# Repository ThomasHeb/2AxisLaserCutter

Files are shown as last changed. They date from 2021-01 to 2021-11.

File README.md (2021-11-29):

## What is new?
- G0 commands for seeking with laser off implemented (for use with Lightburn software)

## What is coming next?
- Please let me know, if you have ideas or need improvements

# 2AxisLaserCutter

- Arduino based CNC laser cutter with display and SD-Card.
- Shared firmware with [4AxisFoamCutter](https://github.com/ThomasHeb/4AxisFoamCutter)
- Ruby Script for SketchUp Make 2017 to generate gcode.

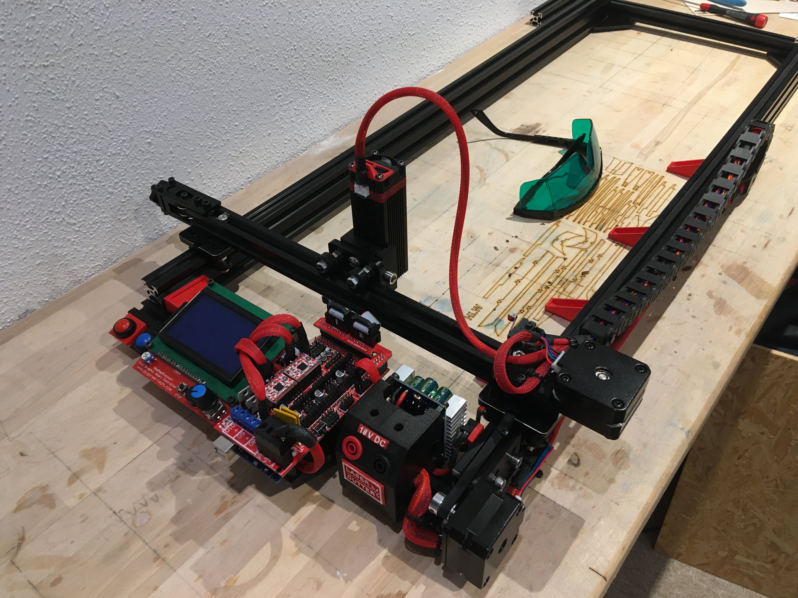
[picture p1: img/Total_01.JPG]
Total_01


My goal was to build semi scale balsa glider based on old fmt plans. It is a lot of effort to copy the plans on the balsa, cut it, and sand it. Especially for small models, very accurate working is necessary. This brought my to the idea to build a laser cutter and do the glider design in SketchUp. 

The base idea ist very simple. Two independent linear axis with NEMA 17 stepper and belts on 2020/2040 v-slot rails and Arduino Mega / Ramps, based on a modified grbl 8c2, which I am using in my FoamCutter, too. There are some special requests for the grbl, when working with a laser, especially when using as an engraver. The firmware modifications will be mentioned in the „Firmware“ section below.

I have a lot old paper plans for gliders. So I take some photos of the plans, imports these to SketchUp Make 2017, redraw and scale the plan. For generating the gcode, I wrote a small script. Description is below in section „Working with SketchUp“.

# Safety
Due to the specific characteristics of laser radiation and the biological and physical effects this has, special protection and cautionary measures are required in the use of lasers.
- Do not look into the beam or direct reflections, also do not look with optical instruments.
- wear special protection googles for the laser you are using
- Clear marking of the laser area with warning signs at all access points.
- Route the laser beam clearly below or above eye level, but not at eye level.
- Refer to the manuals and safety instructions of your laser module
- Refer to the manuals and safety instructions of other used equipment (Ramps, Arduino, DC/DC Converter, power supply, …)
- Please keep all standards and safety topics in mind, when handling with high voltage on power supply, best is to contact an authorised specialist.

# Videos
- [Video tutorial](https://youtu.be/N7kasb9n7cc)

# Mechanics
- 2x linear v-slot actuator with NEMA 17 stepper
- 2020 and 2040 profiles, screws, nuts
- plates for stepper and connecting the profiles 
- Neje Laser
- 3D-printed parts for mounting the hardware on the rails

A bill of material (including hardware and electronics) and detailed photos are in the folder [01_Mechanics](https://github.com/ThomasHeb/2AxisLaserCutter/tree/main/01_Mechanic)

# Hardware

- Arduino Mega with Ramps 1.4 board
- Display and SD card reader for loacl operation

A block diagramm is provided in the folder [02_Hardware](https://github.com/ThomasHeb/2AxisLaserCutter/tree/main/02_Hardware)

# Firmware

- The Firmware is based on GRBL 8c2 
- Special modifications for local operation
- Special operation for synchron power regulation of the laser 

More Details here: [03_Firmware](https://github.com/ThomasHeb/2AxisLaserCutter/tree/main/03_Firmware)

# First operation / setup
In this chapter you find some recommendations how to get started and how to setup the laser cutter.

## First test of Arduino.
The Arduino and the Ramps board are working without the stepper driver or motors.
- Mount the Ramps on the Arduino
- Connect the display to the Ramps
- Connect the Arduino with the USB
- Connect to USB and load the firmware and check if you get a welcome screen (you need an Arduino IDE installed).

## Adjusting and first operation of stepper
- Adjust the driver [link](https://www.makerguides.com/a4988-stepper-motor-driver-arduino-tutorial/)
- Place the jumper and the stepper driver on the Ramps
- Connect the NEMA 17 stepper motor to E0 / E1
- Connect 12V DC to Ramps 3/4
- Connect the Arduino to USB. 
- Go to position menu and check the operation of the stepper motor
- Disconnect power supply and USB

## Operation of limit switches and e-stopp
- Place each a jumper on S and - for X- and X+
- Connect 12V DC to Ramps 3/4
- Optional: Pull one jumper, Arduino should go to Error. Reset the Arduino
- Optional: Pull the other jumper, Arduino should go to Error. Reset the Arduino
- Connect D68 to GND, Arduino should go to Error
- Disconnect power supply and USB

## Mechanic meets hardware
- Assemble the mechanic 
- Connect the hardware
- Do NOT connect the laser
- Wire the NEMA 17 stepper motor
- Optional: Wire the limit switches
- Wire the e-stopp
- Connect 12V DC to Ramps 3/4
- Connect the Arduino to USB. 
- Go to position menu and check movement of the axis
- Check direction of the axis, 
  - Otherwise open the parameters in the Serial Monitor of the Arduino IDE with $$
  - Adjust parameter $7
- Calculate the Steps per mm, adjust parameter $0 and $1
  - Equation is : (USER_STEP_PER_REVOLUTION x USER_MICROSTEPS) / (USER_PITCH_BELT x USER_GEAR)
  - Example: (200 steps/rpm x 16 Microsteps) / (2mm x 20) = 80
  - Best is to adjust the defaults.h, compile and download and set parameter to default with $R
- Operate the e-stopp, Arduino should go to Error. Reset the Arduino
- Optional: Operate the limit switches, Arduino should go to Error. Reset the Arduino
- Optional using limit switches: Go to homing menu and start a homing cycle. 
  - Check if axis are moving to the right direction, otherwise adjust parameter $19
- Check and adjust other parameters. refer to grbl parameter settings online.
- Disconnect power supply and USB

## First operation of the laser
- Assemble and connect the laser
- Operate all the safety measures / steps required, refer to the safety instructions and manuals of your laser
- Connect 12V DC to Ramps 3/4
- Go to position menu and toggle the laser dot. you should see a laser to on your table (0.2% of laser power, you can change this in defaults.h, DEFAULT_LASER_DOT, compiler run and firmware upload is required)
- adjust the focus of the lens of your laser
- Operate the e-stopp, Arduino should go to Error, laser should switch off. Reset the Arduino
- Optional: Operate the limit switches, Arduino should go to Error, laser should switch off. Reset the Arduino
- Optional using limit switches:
  - Go to position menu and toggle the laser dot on.
  - Move the laser to your prefers mechanical zero position.
  - Push the back button (stop button on display)
  - Go to homing menu and select "set as new pull-off?", acknowledge by pushing the rotary knob
  - This position is stored and accessed with the next homing cycle

## Find best settings for the laser
- To achieve good cutting results, you must find the right settings for each material type and thickness
- I recommend to start with a 2mm balsa sheet
  - Take a 1mm balsa sheet and adjust the focus of the laser in the position menu with the dot
  - Make several test cuts with different power settings and feed speeds and repeats
  - A good result is where the complete wood is cut through and corners are sharp
  - My preferred setup is 2xS40F400 (2 repeats with 40% power and a feed rate of 400mm/min), or 3xS40F500, especially when the density of the balsa is a bit higher
  - The resulting dimension is at the beginning not very important, because this can be adjusted in the design.
  - You can use the "test_01.gcode" file from the [06_Example](https://github.com/ThomasHeb/2AxisLaserCutter/tree/main/06_Example) folder (1xS15F500 is used for the text)
  - You can generate your own test pattern with SketchUp and the laser cutter script.
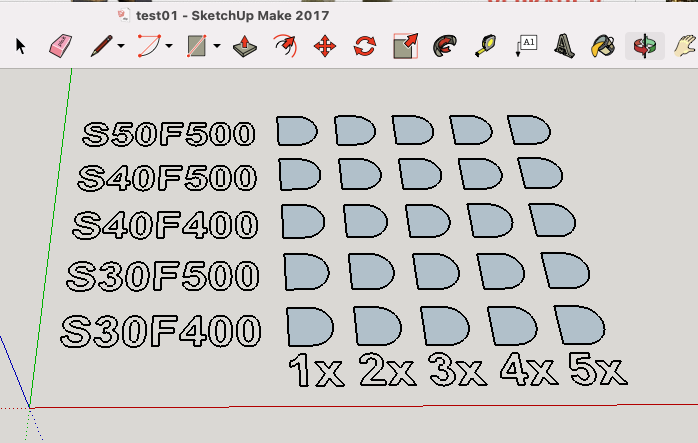
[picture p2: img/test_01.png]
Test_01
    
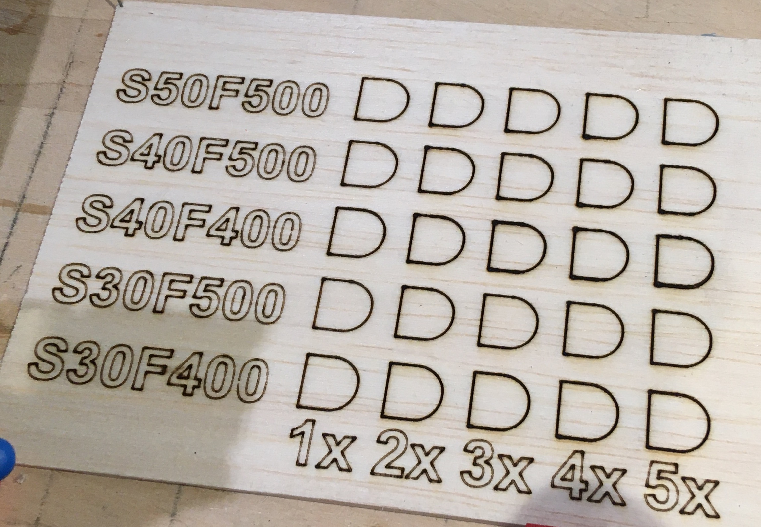
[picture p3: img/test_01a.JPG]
Test_01a
    
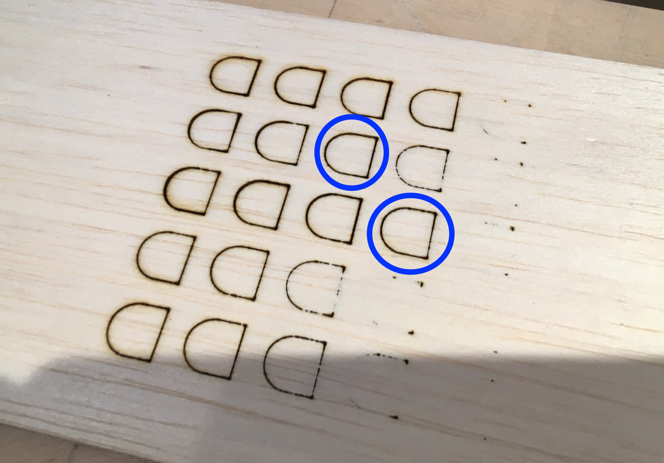
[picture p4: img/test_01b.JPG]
Test_01b
    

# SketchUp Script
I use SketchUp for generating the stl-files for my 3D printed parts. I decided to write a small script which allows me to generate gcode for laser cutting. Currently I use only linear extrapolation in combination. The results are good.

## What you need
- SketchUp (I am using SketchUp Make 2017)
- Ruby Code Editor
- Download lasercutter.rb from the code section

## Functionality and usage of laser.rb
- Download the script from the folder /04_SketchUp/lasercutter.rb
- Open the ruby code editor first and load and execute the lasercutter.rb. This adds 2 menus to the PlugIn menu.
  - LaserCutter Settings: you can define some general settings, like inch/mm, used decimals.
  - LaserCutter Tool: Generates gcode for all selected edges and face surfaces and exports it. 
    - The red axis is used as horizontal
    - The green axis is used as vertical 
    - The algorithm converts surfaces to surrounding edges
    - Searches all edge and generates gcode along the edges
    - There is no algorith for optimizing travel distances

## Check out the tutorial video
- [Video tutorial](https://youtu.be/N7kasb9n7cc)

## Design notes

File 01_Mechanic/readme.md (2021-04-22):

# Mechanics

Total_01

I use 800mm 2040 v-slot rails, which gives me a operation length of app. 680mm (x-axis) and 350mm 2020 v-slot rails, which allows me to travel app. 200mm in depth (y-axis). You can change the length of the rails according to your required working dimensions.
Including stepper, arduino, you might invest app. 340 EUR. For the 3D-printed parts, additional costs have to be considered.
Please be aware, that you can buy laser engraver in complete kits at app. 200 EUR. So I recommend this project only, if it is about building something from scratch.

# Bill of Material
- 2x [800mm 2040 v-slot rail](https://de.banggood.com/Machifit-100-1000mm-Black-2040-V-Slot-Aluminum-Profile-Extrusion-Frame-for-CNC-Tool-DIY-p-1342020.html?ID=527877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)
- 3x [350mm 2020 v-slot rail](https://de.banggood.com/Machifit-Black-2020-V-Slot-Aluminum-Profile-Extrusion-Frame-for-CNC-Laser-Engraving-Machine-p-1341703.html?ID=515970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)
- 4x [90° Connector plate](https://de.banggood.com/Machifit-5-Holes-Aluminum-Profile-Connector-Joint-Plate-Corner-Bracket-for-2020-Aluminum-Profile-p-1350953.html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)
- 2x [NEMA 17 mounting plate](https://de.banggood.com/Machfit-Aluminum-Nema-17-Stepper-Motor-Mount-Plate-for-CNC-Machine-V-slot-Aluminum-Extrusions-Profile-CNC-Parts-p-1470310.html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)
- 2x [Idler pully including plates](https://de.banggood.com/TWO-TREES-Black-2020-Profile-X-axis-Synchronous-Belt-Stretch-Straighten-Tensioner-for-3D-Printer-p-1581141.html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)
- 3x [Gantry Plate](https://de.banggood.com/Machifit-V-Slot-V-Gantry-Plat-Special-Slide-Plate-Five-Roulette-for-2040-Aluminum-Profile-p-1380194.html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)
- 1x Bag [Nuts 5mm](https://de.banggood.com/Drillpro-50pcs-M5-T-Sliding-Nut-Zinc-Plated-Carbon-Steel-T-Sliding-Nut-for-2020-Aluminum-Profile-p-1048439.html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)
- 1x Bag [Nuts 5mm](https://de.banggood.com/Drillpro-100pcs-M5-Hammer-Nut-Nickel-Plated-Carbon-Steel-Aluminum-Connector-T-Fastener-Sliding-Nut-p-1048442.html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)
- 1x Bag [Nuts 3mm](https://de.banggood.com/Drillpro-50pcs-M3-T-Sliding-Nut-Zinc-Plated-Carbon-Steel-T-Sliding-Nut-for-2020-Aluminum-Profile-p-1081131.html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)
- 1x Bag (2 needed) [Limit Switch](https://de.banggood.com/10Pcs-Micro-Limit-Switch-Roller-Lever-5A-125V-Open-Close-Switch-p-945733.html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)
- 1x [red button for stopp operation](https://de.banggood.com/Car-Auto-Momentary-OFF-ON-Push-Round-Button-Horn-Switch-Multicolor-p-927835.html?ID=224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)
- 1x optional [blue button for back operation](https://de.banggood.com/Car-Auto-Momentary-OFF-ON-Push-Round-Button-Horn-Switch-Multicolor-p-927835.html?ID=224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)
- 2x [NEMA 17 Stepper](https://de.banggood.com/17HS4023-12V-Nema-17-2-Phase-Stepper-Motor-For-Extruder-3D-Printer-Motor-p-1368552.html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)
- 1x Pack [Pully 20T + Belt GT2](https://de.banggood.com/20T-GT2-Aluminium-Timing-Pulley-2GT-5M-Belt-For-RepRap-Prusa-Mendel-3D-Printer-p-1081330.html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)
- 1x [Arduino Mega, Ramps 1.4, Stepper Driver](https://www.amazon.de/Drucker-1-4-Controller-Mega2560-R3-A4988-mit-Kühlkörper/dp/B07DJ3WBCP/ref=sr_1_1_sspa?__mk_de_DE=ÅMÅŽÕÑ&dchild=1&keywords=ramps+1.4)
- 1x [Display](https://www.amazon.de/Redrex-Vollgrafik-Display-Controller-3D-Drucker-Arduino/dp/B01LO20XGS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)
- ALTERNATIVE [Arduino, Mega, Ramps 1.4, Stepper Driver, Display](https://de.banggood.com/Geekcreit-LCD-12864-RAMPS-1_4-Board-2560-R3-Control-Board-A4988-Driver-Kit-For-3D-Printer-p-936768.html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)
- 1x [Neje 20W 450nm Lasermodule](https://de.banggood.com/NEJE-20W-Laser-Module-DIY-Kit-450nm-Professional-Continuous-5_5W-Laser-Cutting-Engraving-Module-Blue-Light-with-TTL-or-PWM-Modulation-for-Las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)
- 1x optional [DC DC Converter](https://www.amazon.de/gp/product/B00HV4EPG8/ref=ppx_yo_dt_b_asin_title_o01_s01?ie=UTF8&psc=1)
- 1x optional [red and black connector](https://www.amazon.de/GTIWUNG-Bananenbuchse-Bananensteckdose-Verstärkeranschluss-Bananenstecker)
- optional 3D printed parts, see SketchUp or stl-file in 01_Mechanic folder
- 1x optional [inlay nuts (1 box)](https://www.amazon.de/gp/product/B082KFQV71/ref=ppx_yo_dt_b_asin_title_o03_s00?ie=UTF8&psc=1) for 3D printed parts
- M5, M3, M2.5, M2 screws

# Assembly

You find a lot of pictures in the [img folder](https://github.com/ThomasHeb/2AxisLaserCutter/blob/main/img/).

Recommendation: Connect and wire the hardware (Arduino, Ramps, stepper, laser, …) first and test it. Refer to chapter [„Hardware“](https://github.com/ThomasHeb/2AxisLaserCutter/tree/main/02_Hardware) and chapter „First operation / setup“.

## Y-Axis
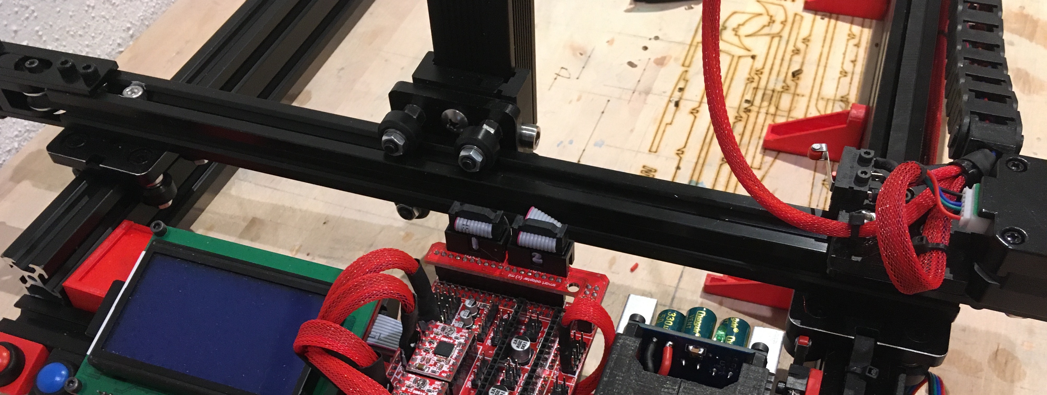
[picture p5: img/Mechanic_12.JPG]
Mechanic_12


### Parts
- 1x 350mm 2020 v-slot rail
- 1x NEMA 17 mounting plate
- 1x Idler pully including plates
- 3x Gantry Plate
- 1x NEMA 17 Stepper
- 1x Pully + Belt
- 1x optional 3D printed "combi holder"
- 1x optional limit switch
- 1x mounting plate for Neje laser (included in laser kit)
- 1x Neje laser

### Steps
- Drill a hole in one gentry plate to fix the laser mounting plate.
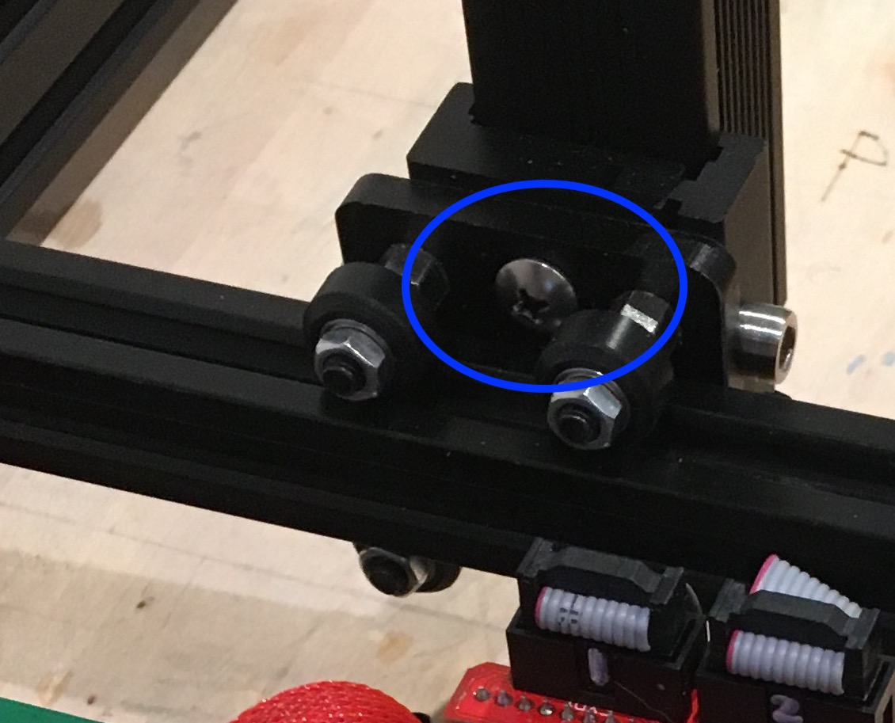
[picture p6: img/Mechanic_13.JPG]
Mechanic_13
  

- Drill a hole in the 2020 v-slot rail to fix the gentry.
- Mount the idler pully.
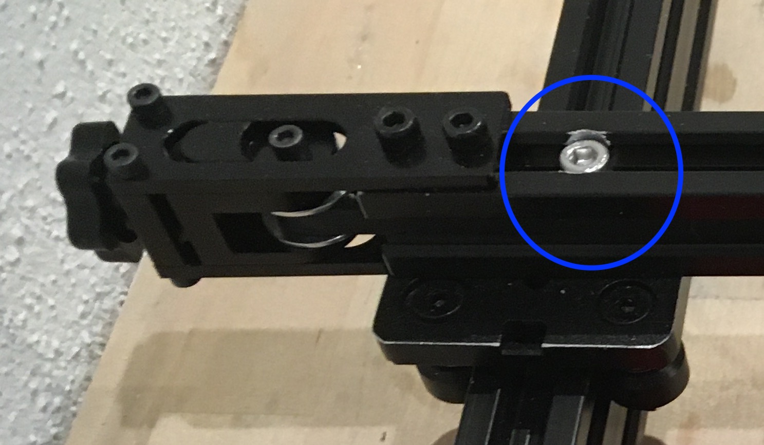
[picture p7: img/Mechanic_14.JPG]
Mechanic_14
  

- Drill two holes (blue) in the 2020 v-slot rail to fix the gentry together with the motor mounting plate
- Optional: Drill two holes (mangenta) in the motor mounting plate and cut a threat to fix the combi holer (3D print)
- Optional: Mount the combi holer (3D print) and the limit switch
- Mount the stepper and the pully and the belt
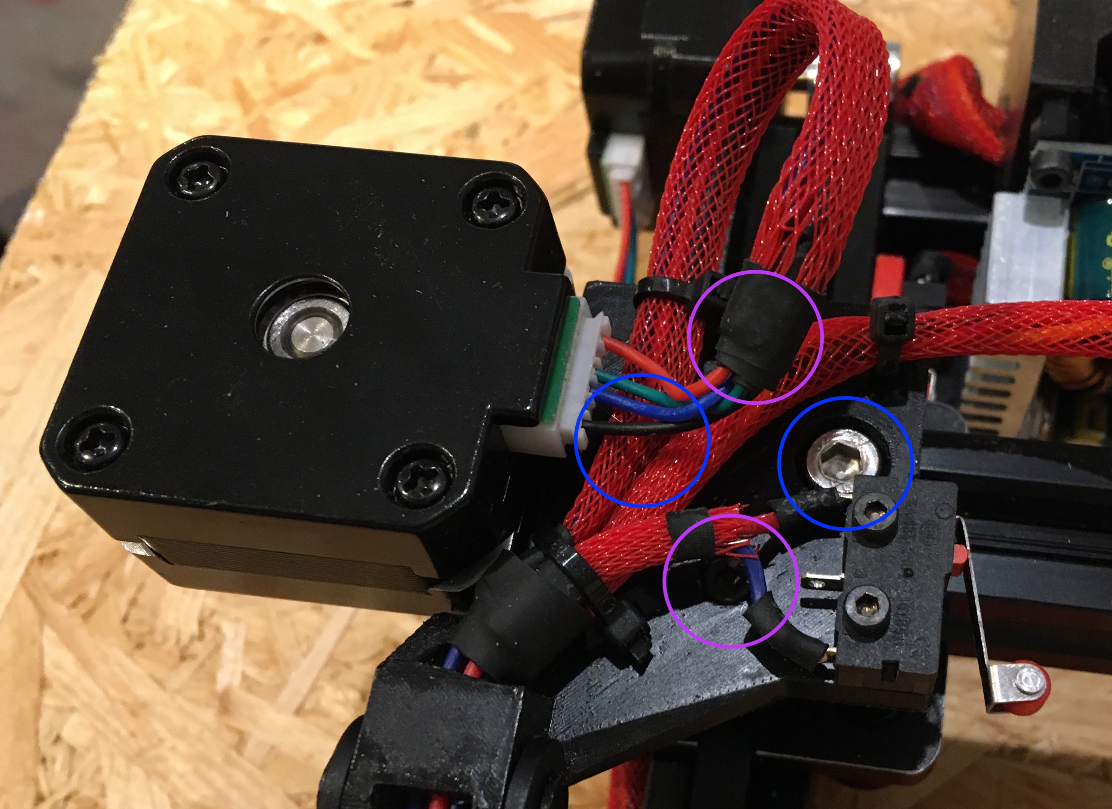
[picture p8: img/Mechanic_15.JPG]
Mechanic_15
  

- You may change the screw for clamping the laser or sand it down a bit, so that the mouinting plate lies flat on the gentry 
- Optional: Mount the cable clamp on the laser (3D print)
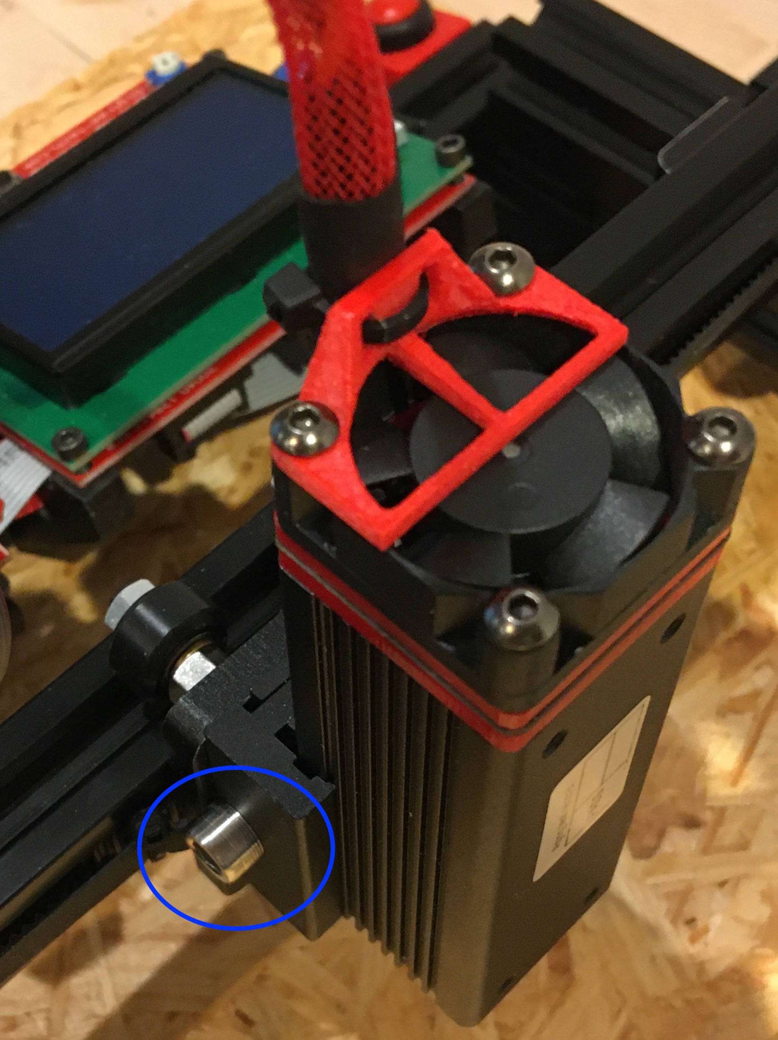
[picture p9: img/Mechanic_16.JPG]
Mechanic_16
  

## X-Axis
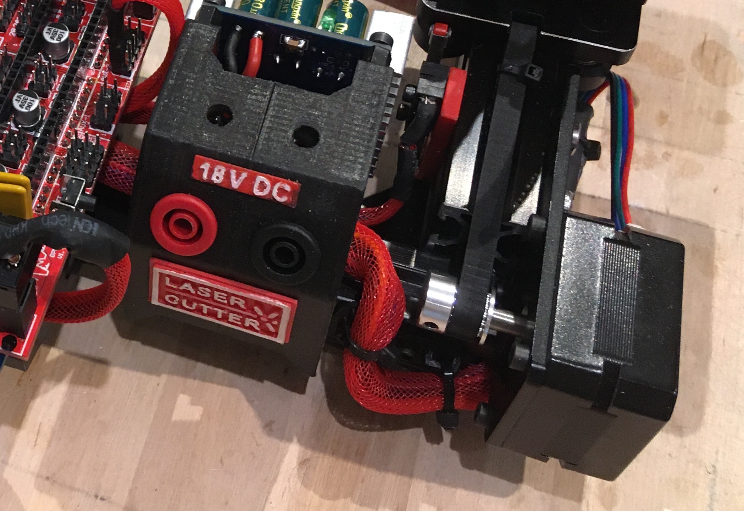
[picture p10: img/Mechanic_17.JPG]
Mechanic_17


### Parts
- 2x 800mm 2040 v-slot rail
- 1x NEMA 17 mounting plate
- 1x Idler pully including plates
- 1x NEMA 17 Stepper
- 1x Pully + Belt
- 1x optional 3D printed "holder cable chain"
- 1x optional 3D printed "holder limit switch"
- 1x optional limit switch

### Steps
- Mount the motor plate with the NEMA 17 stepper
- Add the Y-Axis
- Mount the idler pully.
- Optional: Mount the limit switch and the limit switch holder
- Optional: Mount the holder for the cable chan and the cable chain itself
- Mount the pully and the belt
- Add the second 800 v-slot rail to the idler gentry
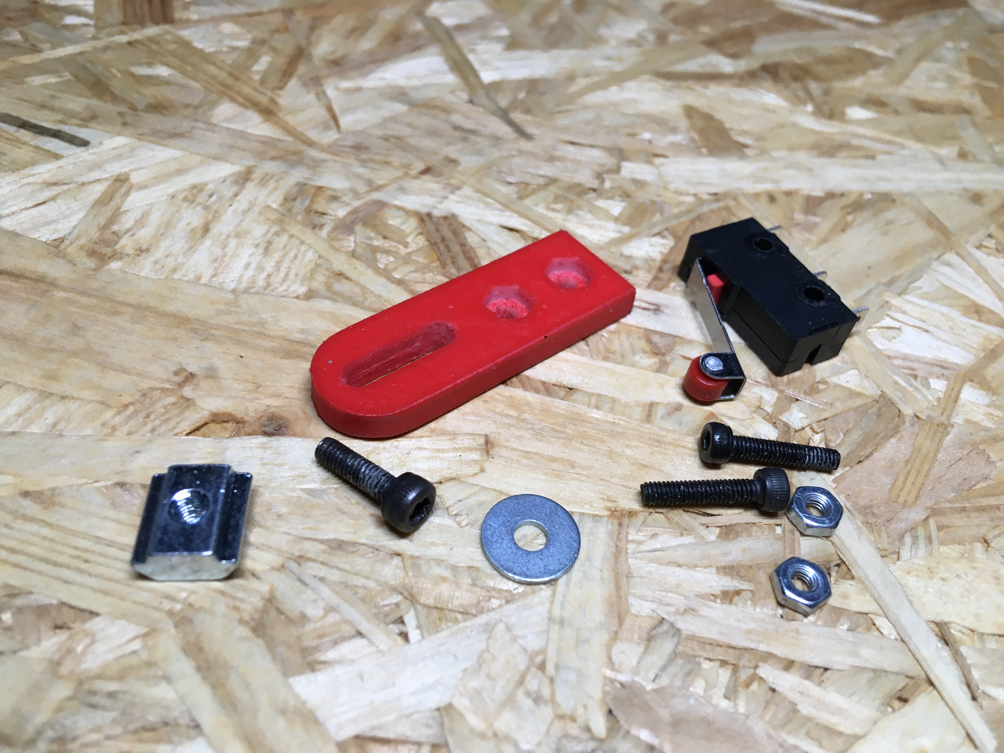
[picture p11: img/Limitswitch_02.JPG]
Limitswitch_02
  
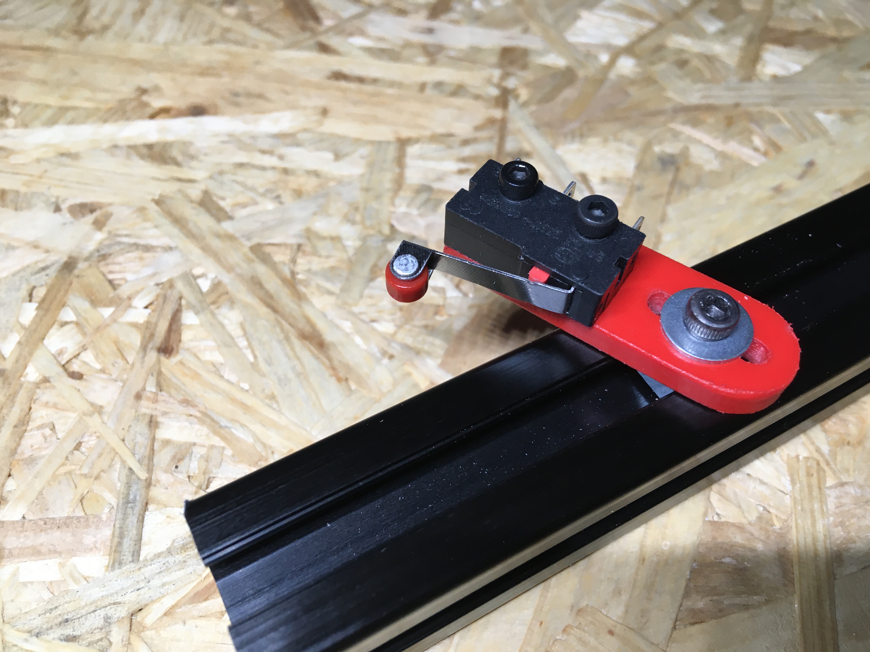
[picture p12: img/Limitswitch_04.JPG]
Limitswitch_04
  
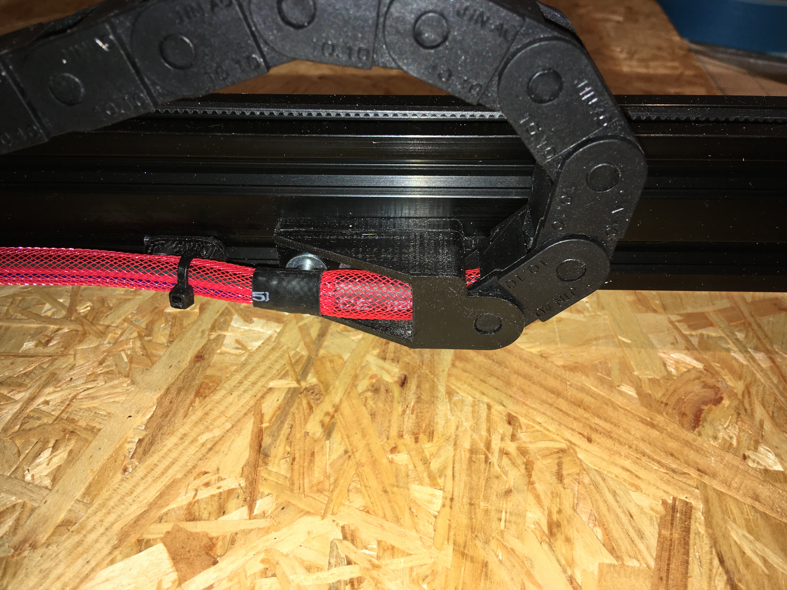
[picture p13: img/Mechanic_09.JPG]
Mechanic_09
  

## Connection rails with electronic
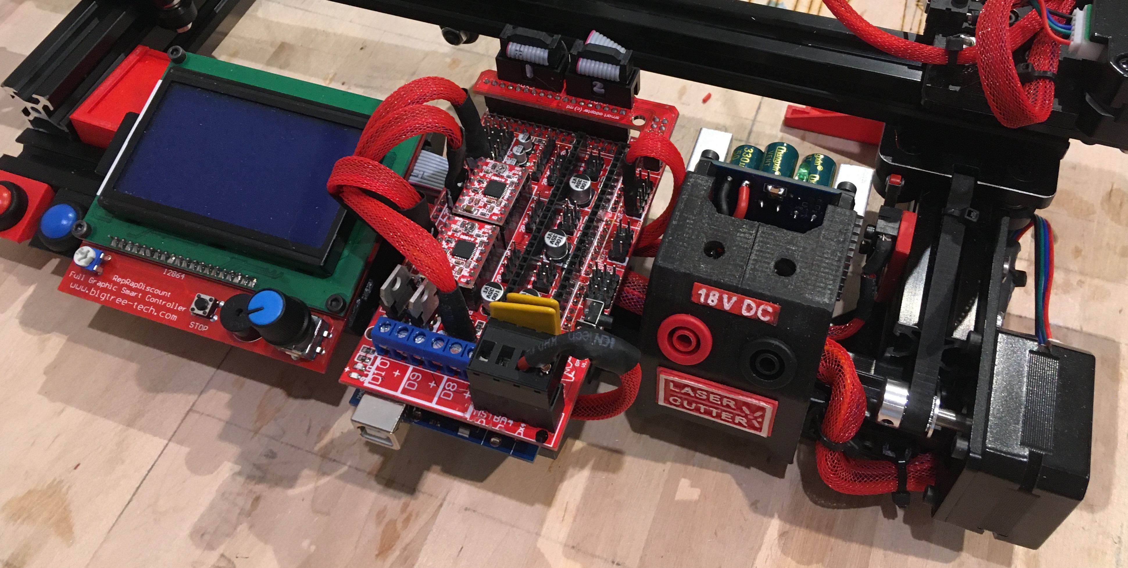
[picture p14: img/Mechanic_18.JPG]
Mechanic_18


### Parts
- 2x 350mm 2020 v-slot rail
- 4x 90° Connector plate
- 1x Arduino Mega
- 1x Display
- 1x Ramps
- 1x optional DC DC Converter
- 1x optional red and black connector
- 1x optional blue button
- 1x red button
- 3D printed holder with inlay nuts

### Steps
- Mount the 90° connector plates on the edges of the 800mm 2040 v-slot rails
- Connect the two rails with a two 350mm 2020 v-slot rails (these rails need to be cut)
- Next to the motor mounting plate of the x-Axis: Make some space for the screw
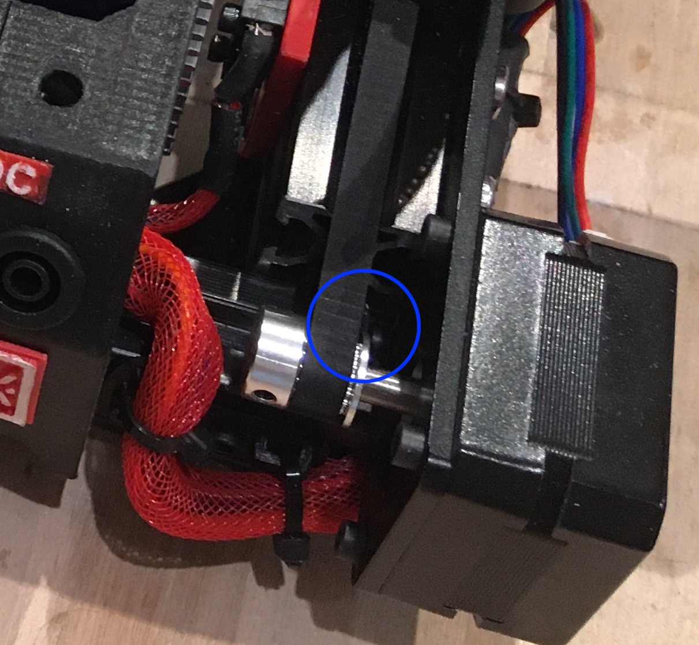
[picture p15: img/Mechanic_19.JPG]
Mechanic_19
  
- Mount the 3D printed holders for display, buttons, Arduino/Ramps and power connection (different options available, see SketchUp file / stl-files)
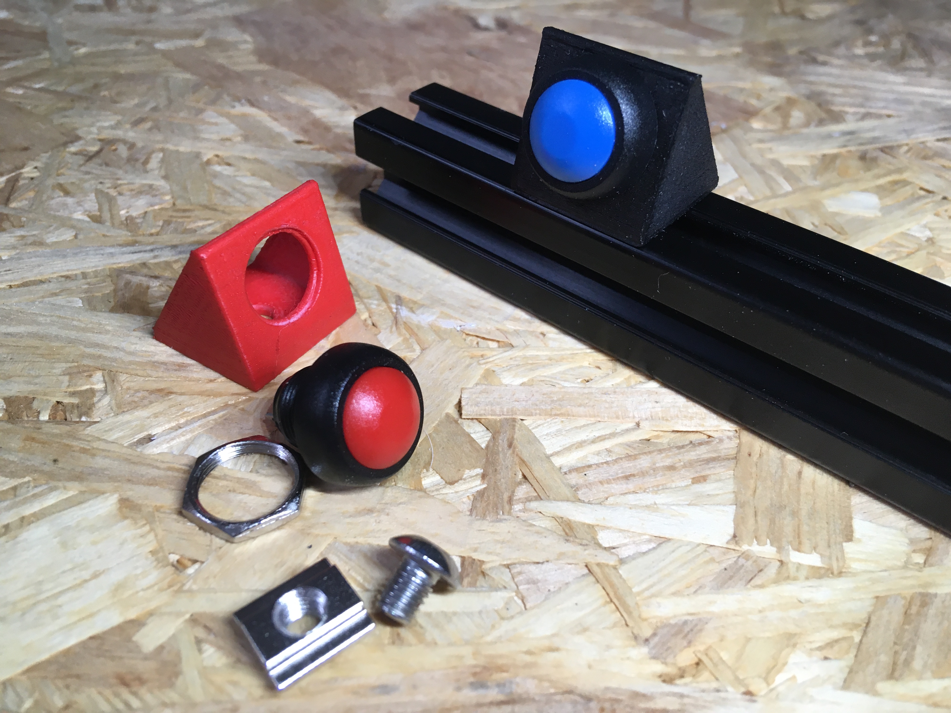
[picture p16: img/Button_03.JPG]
Button_03
  
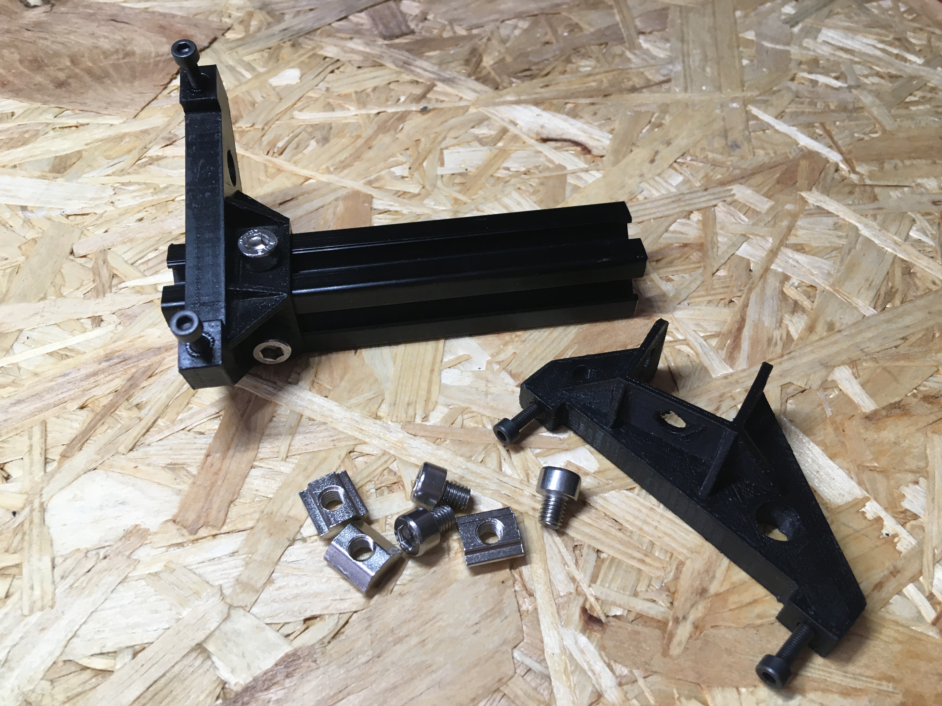
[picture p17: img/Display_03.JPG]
Display_03
  
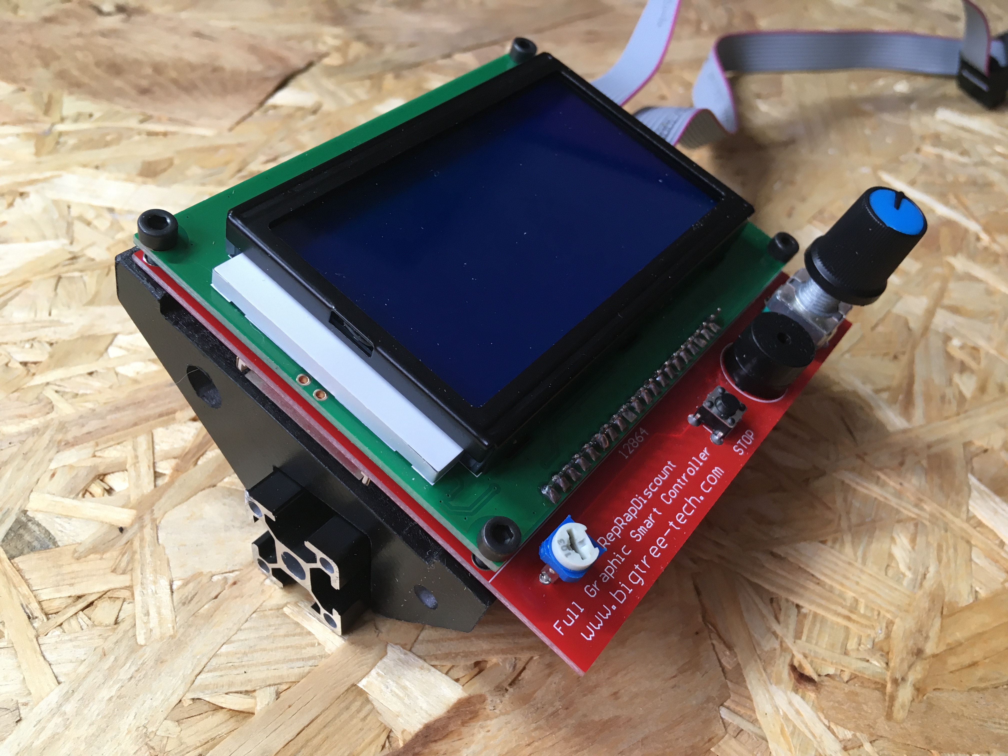
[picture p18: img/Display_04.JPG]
Display_04
  
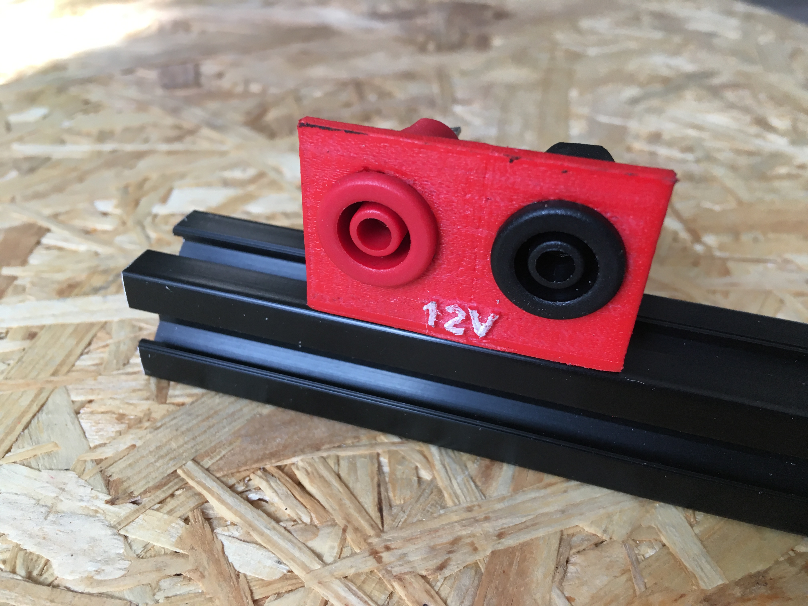
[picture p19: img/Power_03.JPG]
Power_03
  
- For wiring, see Section [02_Hardware](https://github.com/ThomasHeb/2AxisLaserCutter/tree/main/02_Hardware)

## Final
Before tightening all screws, please ensure that all axis and the laser it self are orientated in a 90° angle, all movements are smooth.

[Back to main page](https://github.com/ThomasHeb/2AxisLaserCutter)

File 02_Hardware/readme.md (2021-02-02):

# Hardware

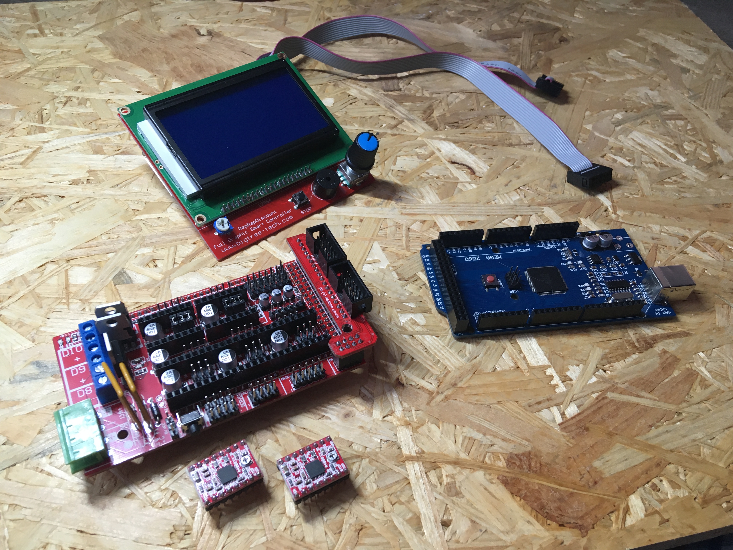
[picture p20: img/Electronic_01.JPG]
Electronic_01


The hardware is based on Arduino Mega with display and Ramps 1.4 Board. Ramps 1.6 and similar boards will work, too.

# Modifications
- Add a 100nF C between S and GND for the X and Y limit switches
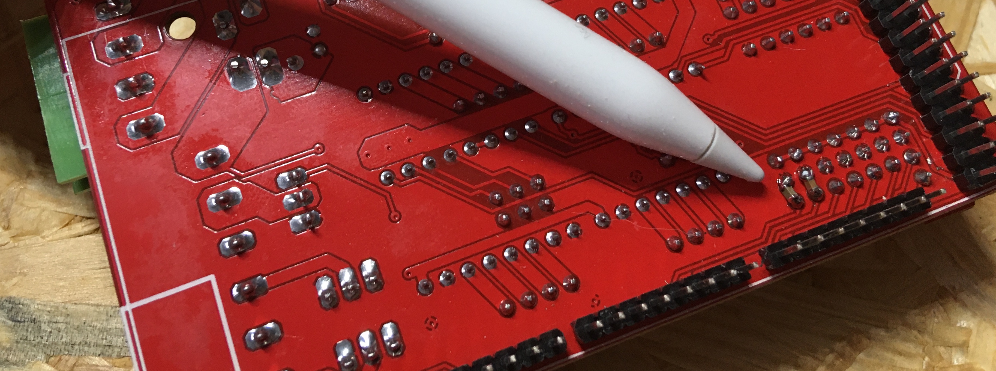
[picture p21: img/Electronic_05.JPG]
Electronic_05
  
- Add a 100nF C between D63 and GND for the e-stopp button
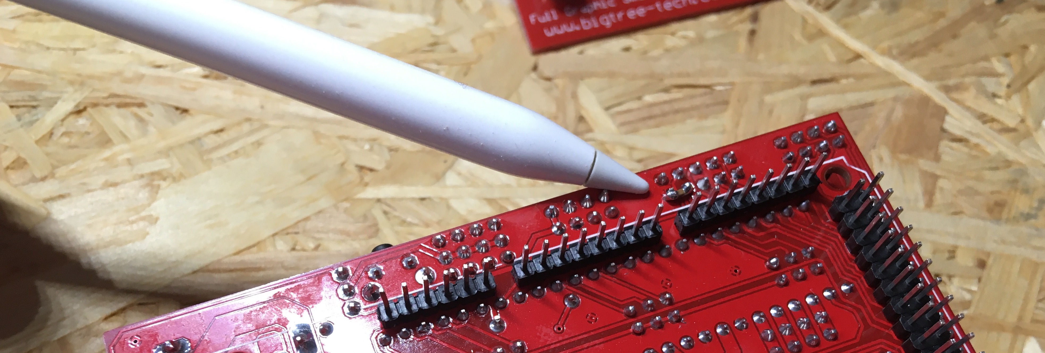
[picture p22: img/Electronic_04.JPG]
Electronic_04
  

- Optional: When using an external back button, connect the button by soldering wires parallel to the stop button on the display, otherwise the stop button on the display operates as back button.

# Blockdiagram / Connections

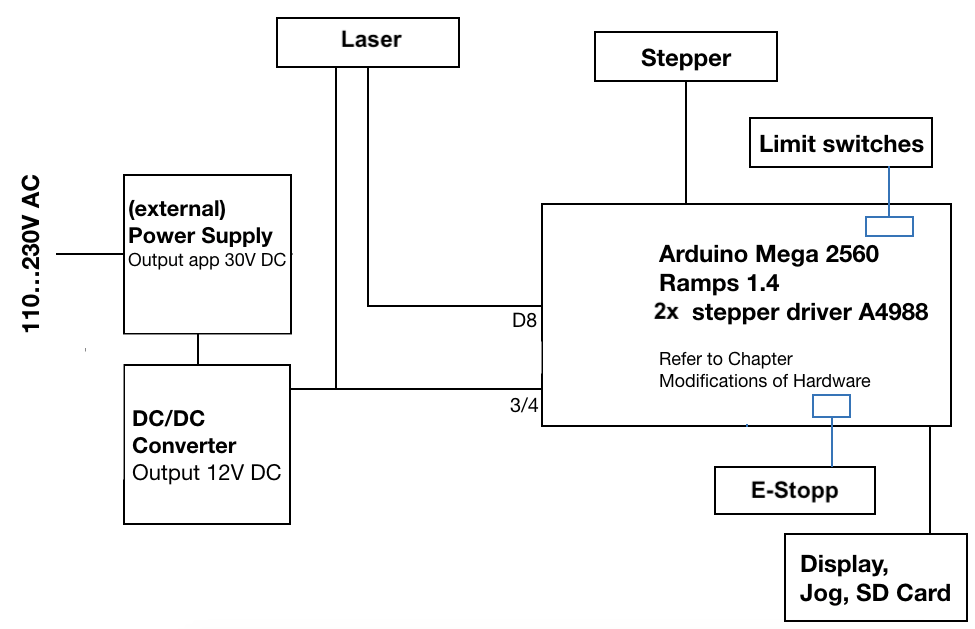
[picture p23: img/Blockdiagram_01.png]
Blockdiagram_01
  
- Stepper X-axis on E0 socket on Ramps // 1/16 Microsteps (set all three jumpers)
- Stepper Y-axis on E1 socket on Ramps // 1/16 Microsteps (set all three jumpers)
- Optional limit switch X-axis on X- S/- on Ramps (1st from left, top view)
- Optional limit switch Y-axis on X+ S/- on Ramps (2nd from left, top view)
- E-Stopp: D63 / GND
- Laser PWM: directly to D8 from Arduino 
  For Neje Laser: Do not use the MOSFET on Ramps / Do not use connect the laser to the terminal screws. Refer to user manual of your laser!
  On Arduino Pin D8 a PWM Signal is available to control the laser. You may connect the laser directly or with a small amplifier to that pin. Please refer to Arduino Mega / Ramps schematic / pcb layout.
- Optional: Use a DC/DC Converter with 12V output voltage to supply the Arduino / Laser
- Power supply:
  - You may use any power supply, such as laboratory power supply, to operate the setup.
  - Optional: DC/DC Converter to have a stabilised fixed voltage (I use this supply, because I have many machines operating with up to 30V. So even when I connect a 30V power supply, everything is operating fine, because of internal DC/DC regulation). You can set the output voltage to any voltage between 9…17V (operation voltage for Arduino and Ramps/Stepper), as long as it fits to your laser, too. My Neje laser operates with 12V as shown in the block diagram.
  - The block diagram above shows my favourite setup with a single power connection for my external laboratory supply, a DC/DC converter to supply the laser and the Arduino. Typical less than 2,5 A are required.

  - This block diagram shows an external power supply to operate the laser with a different voltage level as for the Arduino. The DC/DC converter supply the Arduino. Advantage is that you still have only one external power supply. Be aware, for Neje laser Arduino and laser must have the same ground level, please connect GND of the laser to GND of Arduino, too. Be aware that changing the voltage level for the laser may regulate it’s power, too. This means you have to adjust your settings (refer to First operation / setup). The block diagram shows a laser operating at app. 30 VDC
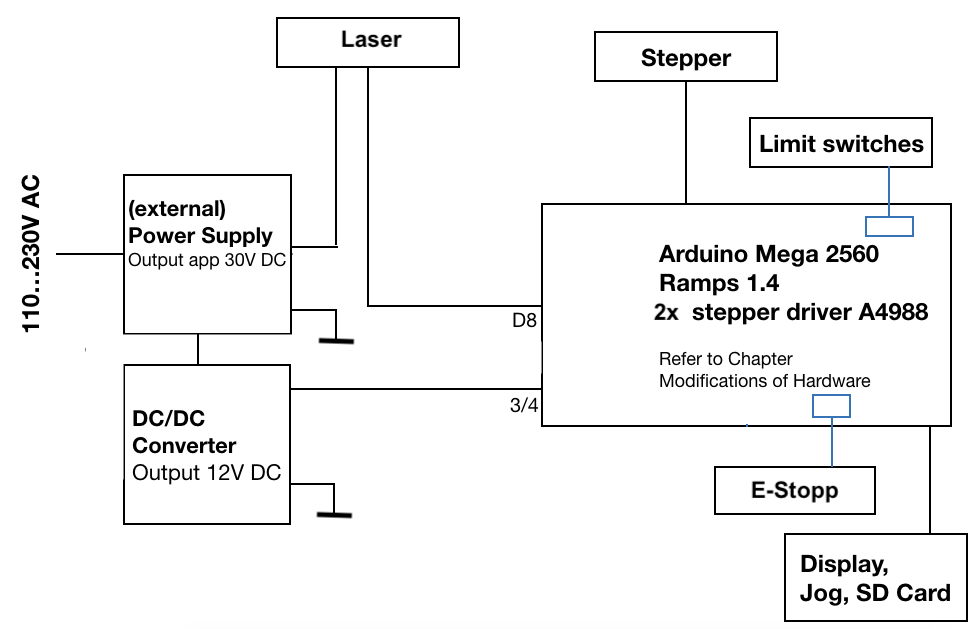
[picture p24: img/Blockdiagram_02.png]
Blockdiagram_02
  

  - This block diagram shows the operation with two different power supplies. One is set to 9….17V DC to supply the Arduino. The other operates the laser. Be aware, for Neje laser Arduino and laser must have the same ground level, please connect GND of the laser to GND of Arduino, too. Be aware that changing the voltage level for the laser may regulate it’s power, too. This means you have to adjust your settings (refer to First operation / setup).
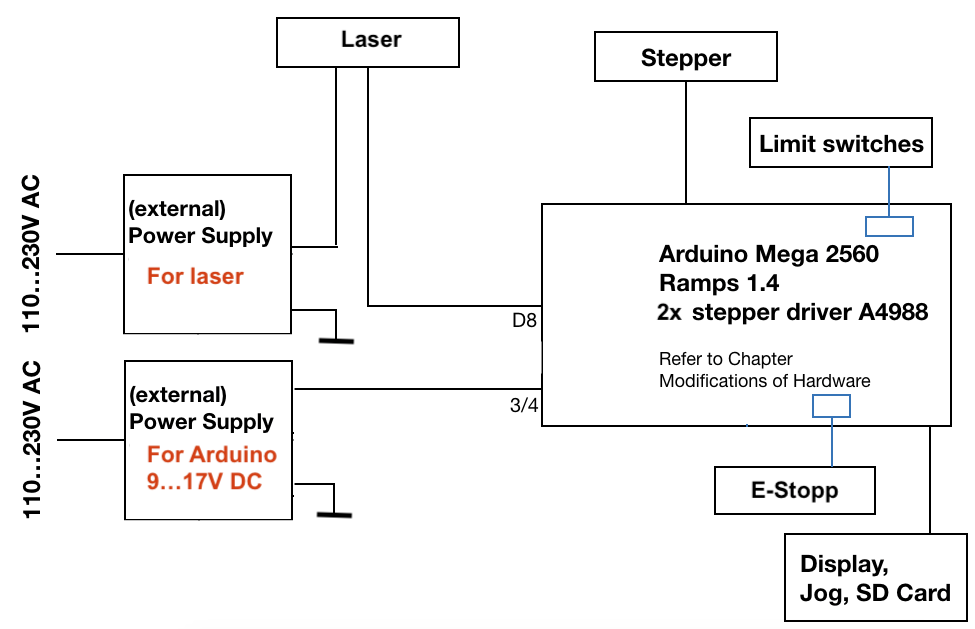
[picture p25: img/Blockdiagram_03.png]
Blockdiagram_03
  

[Back to main page](https://github.com/ThomasHeb/2AxisLaserCutter)

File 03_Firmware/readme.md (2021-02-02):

# Firmware
The firmware is based on the grbl version 8c2 modified for foam cutter and laser cutter. 
A modified version of U8G2 library for the display and SdFat for SD card reader is used.

Links to the original 
- [grbl 8c2 foam](https://www.rcgroups.com/forums/showthread.php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)
- [U8G2 Lib by Oli Kraus, tested with version 2.27.6](https://github.com/olikraus/u8g2)
- [SdFat by Bill Greiman, tested with version 1.2.3](https://github.com/greiman/SdFat)

Many thanks to you, for writing and sharing this fantastic code.

The firmware is a common project with [4 Axis Foam Cutter](https://github.com/ThomasHeb/4AxisFoamCutter).
Download the git from [4 Axis Foam Cutter](https://github.com/ThomasHeb/4AxisFoamCutter) and use the firmware / librarys from the subfolder 

### Major changes to FoamCutter firmware
- Tool syncronisation a spindle or a hotwire is not very fast... it needs time to reach target rpm or target temperature
  - A spindle or a hotwire is not very fast... it needs time to reach target rpm or target temperature
  - So tool commands are not synchronised with grbl line execution, because you normally start the tool with M3 followed with a pause G4P3. The pause command will synchronise the execution.
  - Using a laser requires laser synchronisation with movement within one gcode line, (especially if you are working with different shades)
  - Tool synchronisation is included for Laser and Foam Cutter. You should still use pause commands for Foam Cutter to give some time to heat up. Laser Cutter operates gcode by switching on the laser with M3 and controlling it’s power wir S0…100 in each gcode line. 
  - power control during ac/deceleration is not implemented yet. So good settings for grbl is fast ac/deceleration, medium speed (400 - 600 mm/min are tested), and medium laser power.
- E-stopp is always active / other buttons are not supported
  - Laser cutter has only two axis and manual operation of the laser is a safety issue.
  - Position menu is operated with knob and back button (marked as stop on display) only.
  - Laser can not be operated manually, only a focusing dot is available in position menu.
  - E-stopp on pin D63 is always active - it does not match the standards for safety! Please ensure additional measure, i.e interrupting main power supply.
  - Other buttons are not implemented
- Common tool control
  - implementation of hotwire is moved to tool to offer common tool control interface (hotwire and laser use same interface)
- Compiler switches
  - Select the version LASER_CUTTER in config.h file
  - Separated default settings in defaults.h.

### How to install:
- Download the firmware / library from [4 Axis Foam Cutter](https://github.com/ThomasHeb/4AxisFoamCutter)
- Install (Copy!) the libraries from /03_Firmware/libraries directly in your ../Arduino/libraries/ folder (prefered, because updates of the original libraries may cause problems with grbl)
- You may delete other versions of this libraries first
- Select the version LASER_CUTTER in config.h file
- Compile and download.

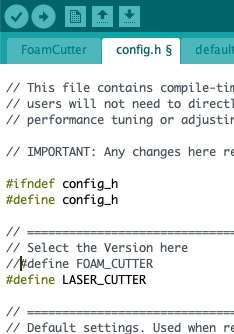
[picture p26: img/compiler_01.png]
compiler_01


### Changes within the library U8G2 - only for information:
Grbl uses almost all resources of the Arduino to control the stepper within an accurate timing. So the standard approach of Arduino is not working any more, because some resources are not available anymore for the Arduino framework. Within the U8G2 I use a software driven SPI on pin D50 to D52 (I didn’t check, if hardware driven SPI would work, too). The only thing I needed to change, was the required delay within the SPI. Therefore I changed the delay function to the grbl supported delay function.

### LCD, SD card and buttons, ….
The LCD display, rotary knob and back buttons (marked as stop on the display)  are controlled inside the lcd.h and lcd.cpp. Knob and button are read within the lcd_process(), from where all processing functions of the sub menus are called.
Functions within the sub menus, which are related to cnc functionality are called as if they would have been called via UART/USB. So you will get an ok over the UART/USB for a local called cnc command, too. The firmware can still be controlled with gcode sender tools via the UART/USB.
SD card is processed inside lcd.cpp and lcd_process(), too. Processing of the SD card is handled with a state machine, which reads the selected file char by char, similar as reading the UART. 
During processing a file from SD card, button are ignored, operation can only be stopped with an IRQ of the limit switches or the e-stop.

Please have a lock at the parameters (command $$ over Serial Monitor)
Information of how to get started are [HERE](https://github.com/ThomasHeb/2AxisLaserCutter#first-operation--setup).
Please search the web for more detailed grbl parameter settings.

### Functions on local display / buttons
- e-stop: IRQ based local stop, this does not match the requirements of any safety standard.
- Idle stepper
- Homing (only available if limit switches are used)
  - homing including pull-off
  - set current position as new pull off position: This function is used to travel from limit switches to machine zero position. Adjust the position with the position menu
- Position menu
  - adjust each axis independent
  - set or travel to a temporary home position
  - set or travel to a temporary zero position
  - select the axis and step size with the knob. By pressing the knob, you can move the axis by rotationg the knob.
  - toggle the laser point (by default 0,2% of maximum power, see defaults.h, DEFAULT_LASER_DOT). You can use this to focus the laser. 
- SD-Card
  - read file list from SD-Card (only with defined file extensions (config.h), only from root directory, keep filenames short)
  - valid gcode file extensions: .nc, .gcode (you may change the file extension to oneof these)
  - execute a file from the SD-Card
  - visualise the progress (bytes read and send to gcode processing, not bytes really executed)
- The firmware can still be controlled with gcode sender tools via the UART/USB 

### How to start:
Please refer to grbl documentation for parameter settings and first steps. A good point to start is shown [HERE](https://github.com/ThomasHeb/2AxisLaserCutter#first-operation--setup)

[Back to main page](https://github.com/ThomasHeb/2AxisLaserCutter)

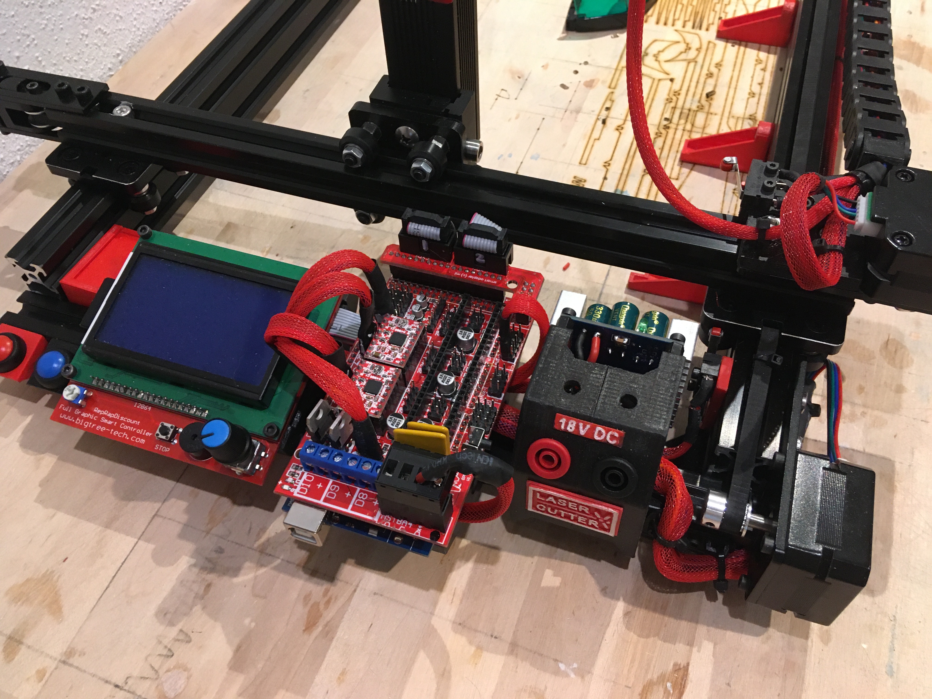
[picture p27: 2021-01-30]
img/Mechanic_11.JPG

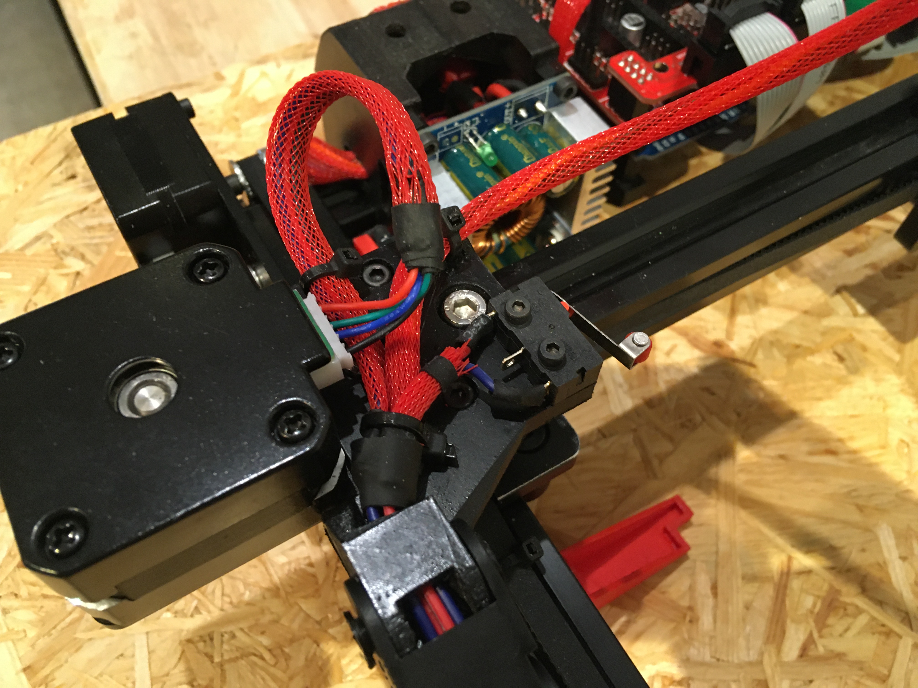
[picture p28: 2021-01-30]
img/Mechanic_06.JPG

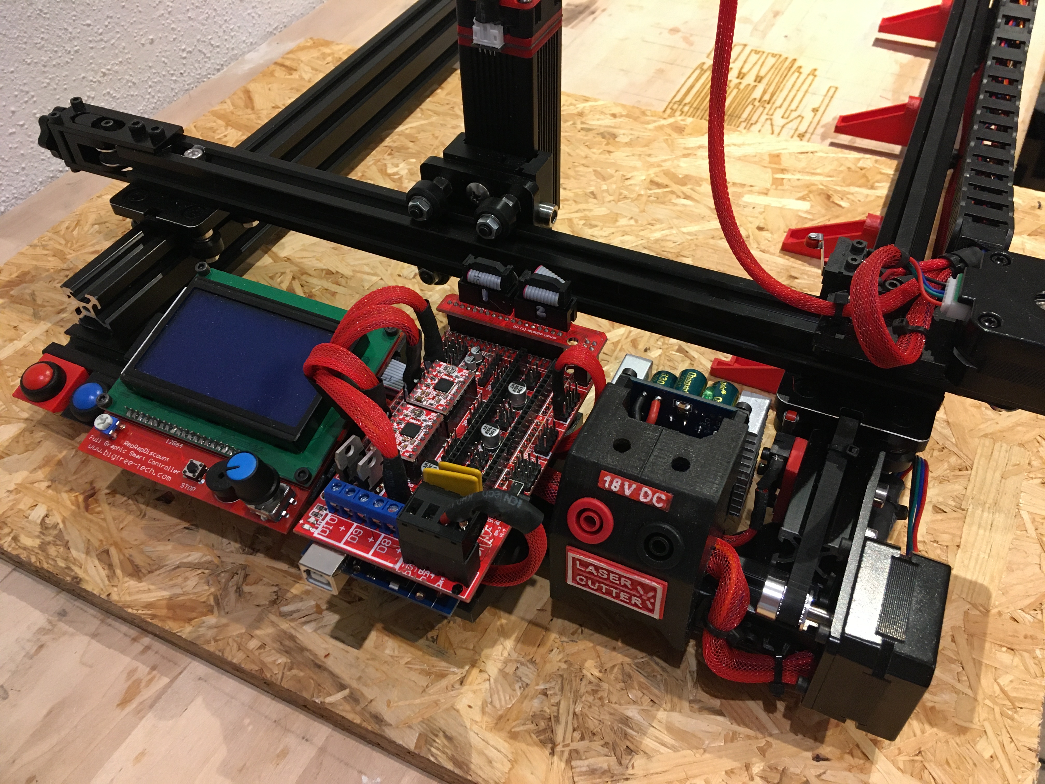
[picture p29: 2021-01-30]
img/Mechanic_02.JPG

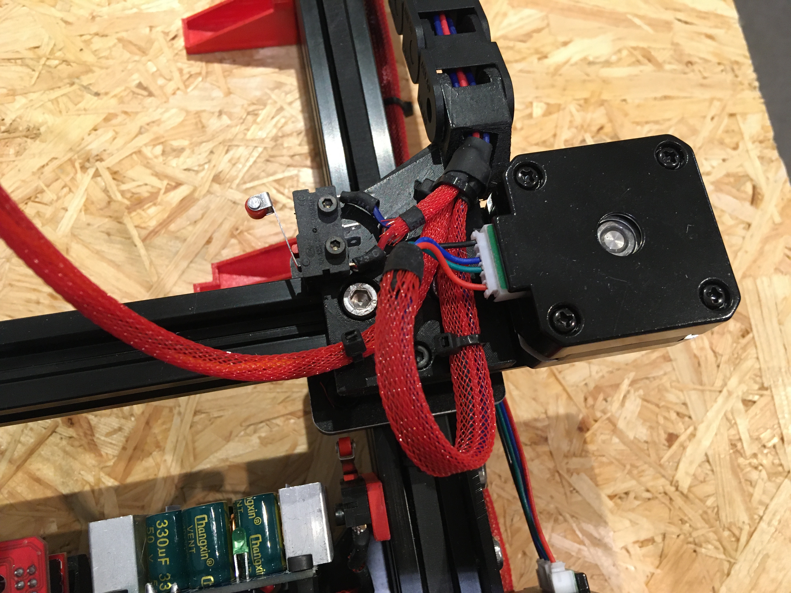
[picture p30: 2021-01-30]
img/Mechanic_04.JPG

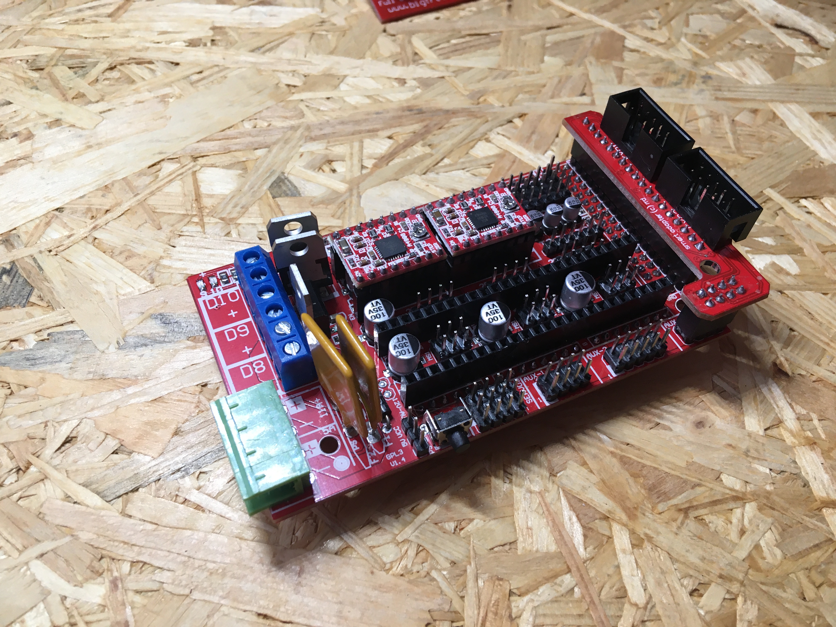
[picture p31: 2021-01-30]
img/Electronic_03.JPG

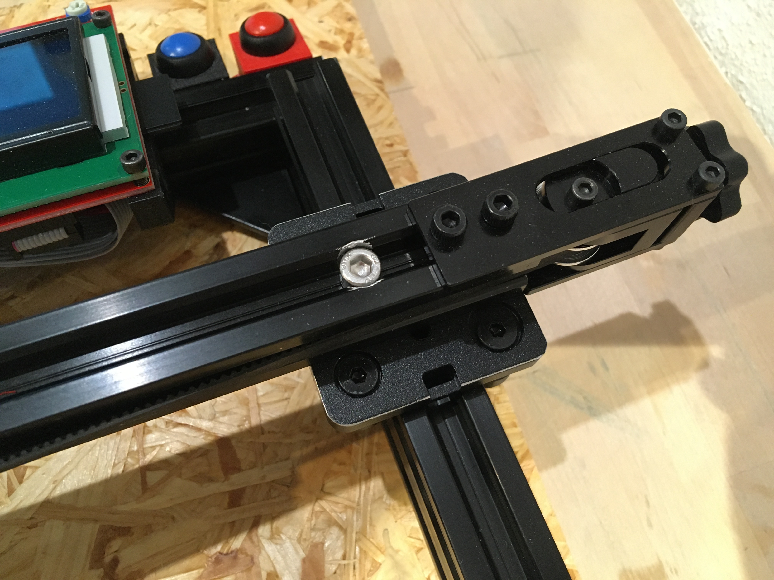
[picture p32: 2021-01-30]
img/Mechanic_08.JPG

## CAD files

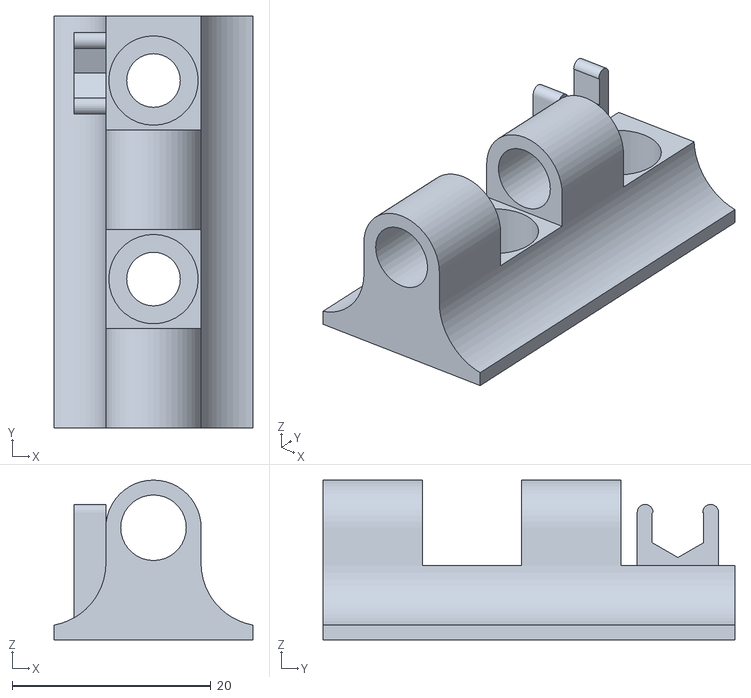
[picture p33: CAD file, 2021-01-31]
01_Mechanic/Holder_Inbus_1.stl
20.0 x 41.5 x 16.1

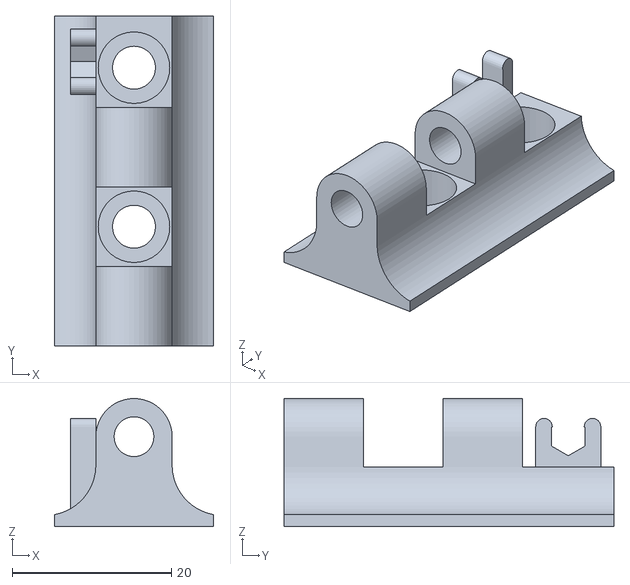
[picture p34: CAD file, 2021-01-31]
01_Mechanic/Holder_Inbus_2.stl
20.0 x 41.5 x 16.1

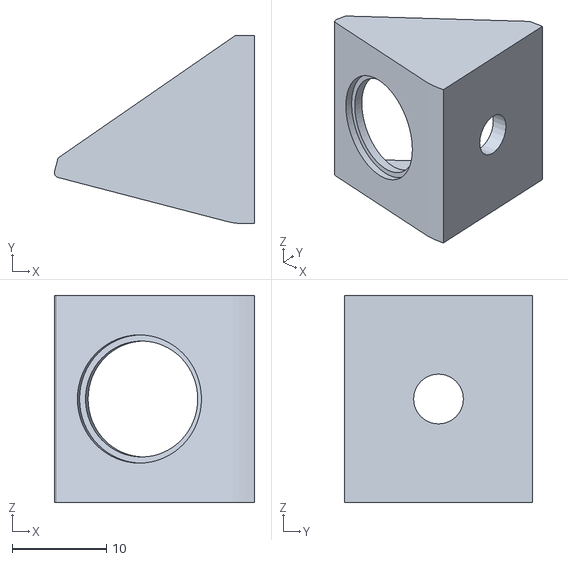
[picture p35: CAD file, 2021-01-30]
01_Mechanic/Holder_Button.stl
21.2 x 20.0 x 22.0

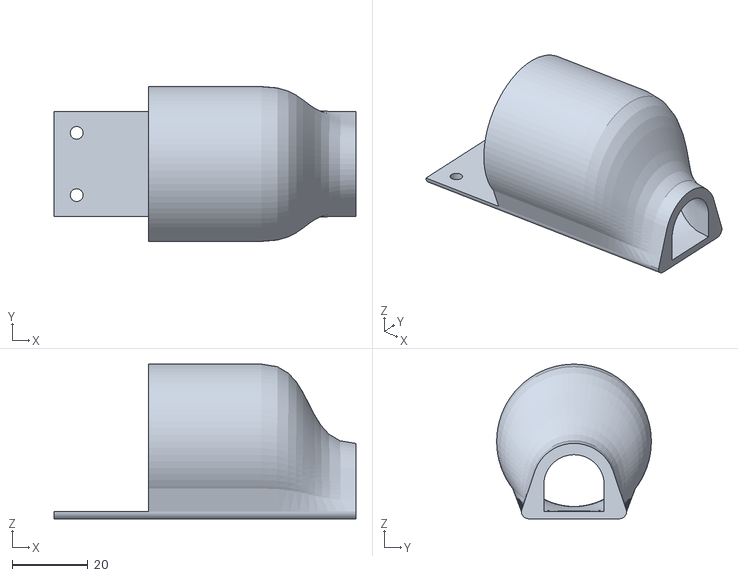
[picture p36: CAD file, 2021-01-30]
01_Mechanic/Suction_2.stl
80.0 x 41.0 x 41.0

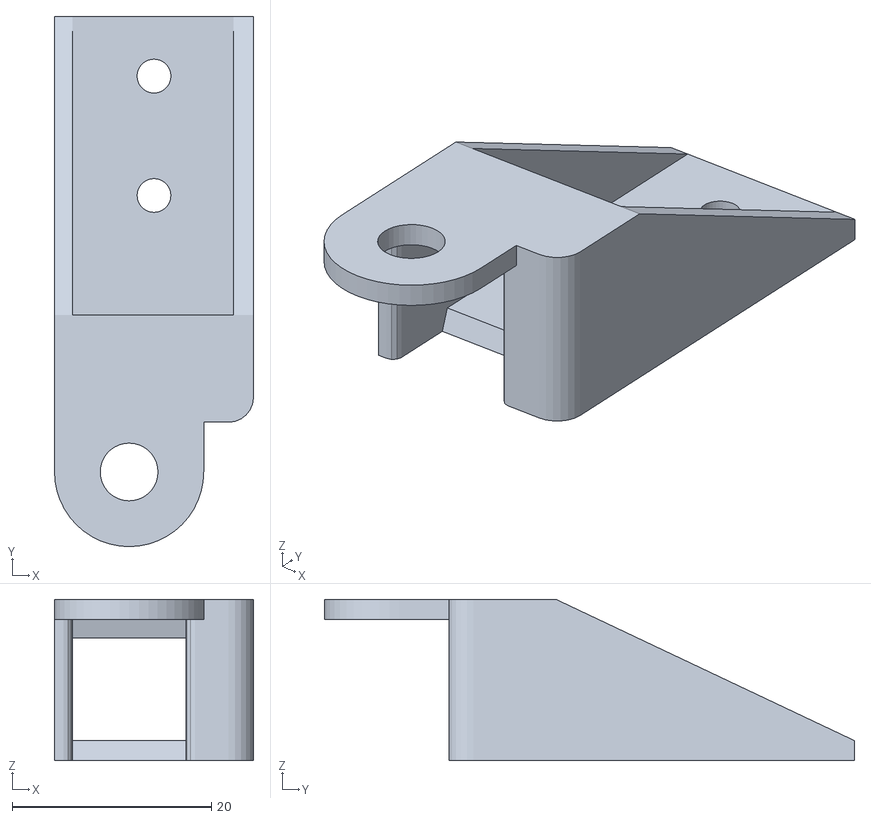
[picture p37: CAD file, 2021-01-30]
01_Mechanic/Holder_Cablechain_Top.stl
20.0 x 53.3 x 16.2

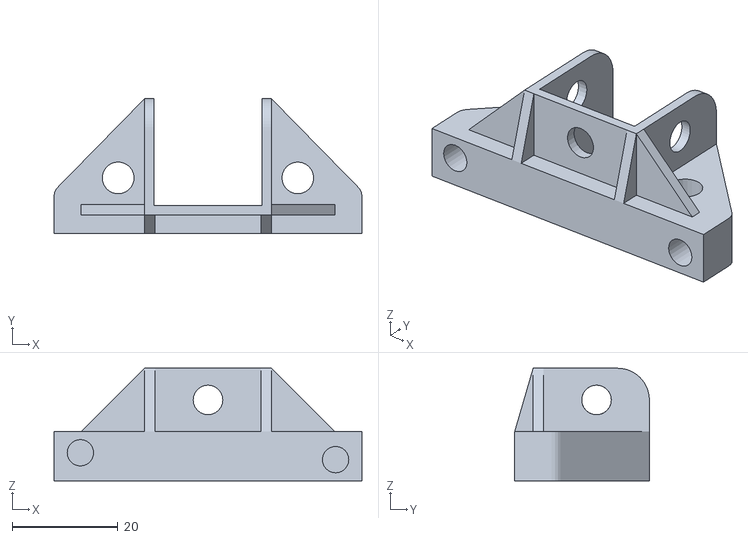
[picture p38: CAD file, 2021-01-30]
01_Mechanic/Holder_Arduino_L.stl
58.3 x 25.5 x 21.3

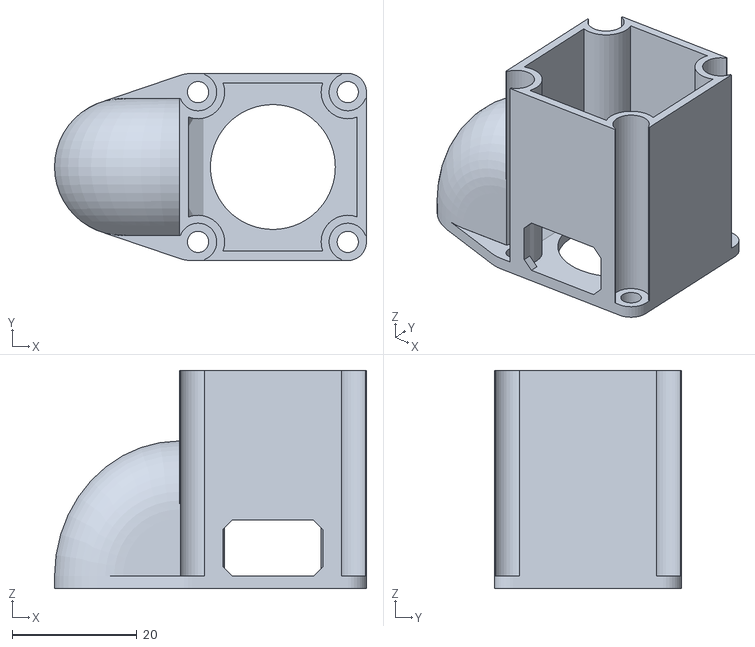
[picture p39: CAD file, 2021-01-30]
01_Mechanic/Suction_1.stl
50.0 x 30.0 x 35.0

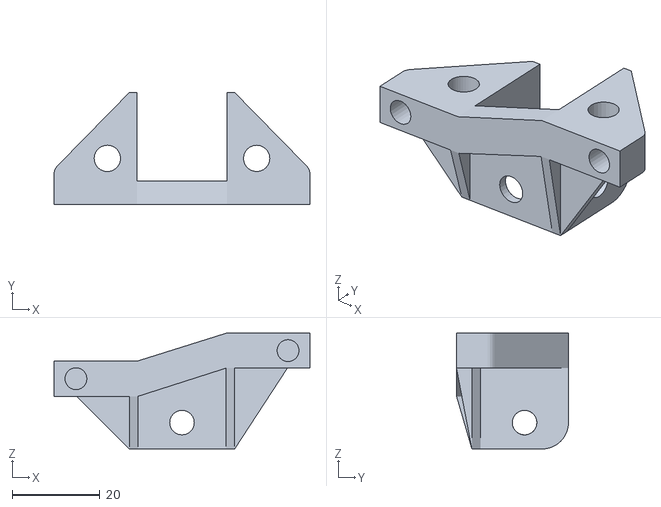
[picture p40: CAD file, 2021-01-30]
01_Mechanic/Holder_Arduino_R.stl
58.3 x 25.5 x 26.4

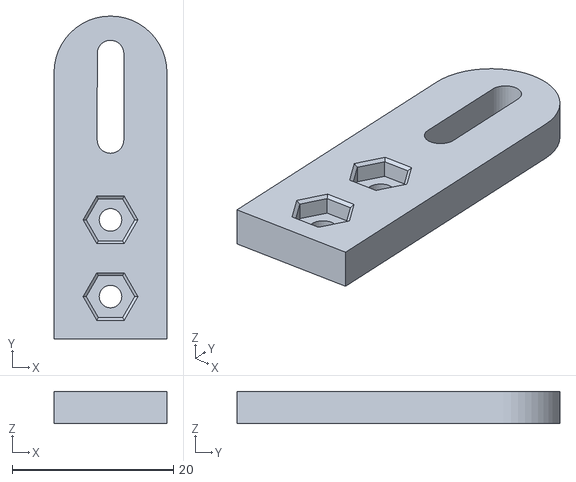
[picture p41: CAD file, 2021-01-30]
01_Mechanic/Holder_Limitswitch.stl
14.0 x 40.0 x 4.00

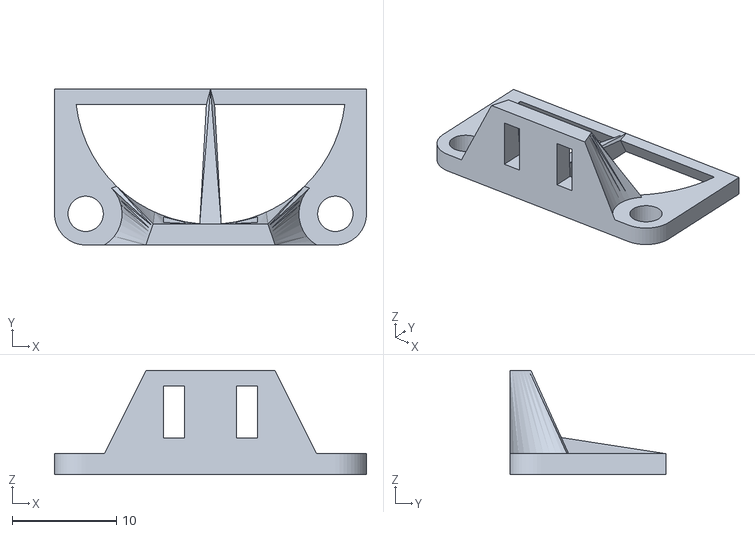
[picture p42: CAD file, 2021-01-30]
01_Mechanic/Cable_Clamp_Laser.stl
30.0 x 15.0 x 10.00

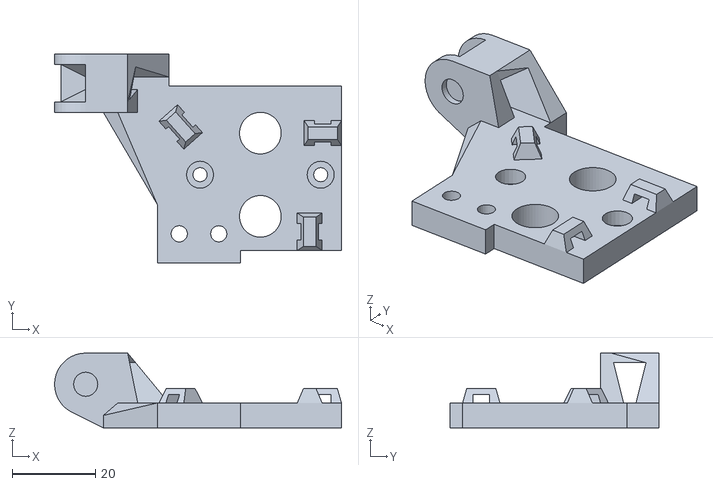
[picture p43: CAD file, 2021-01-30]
01_Mechanic/Holder_Combi.stl
69.0 x 50.2 x 18.0

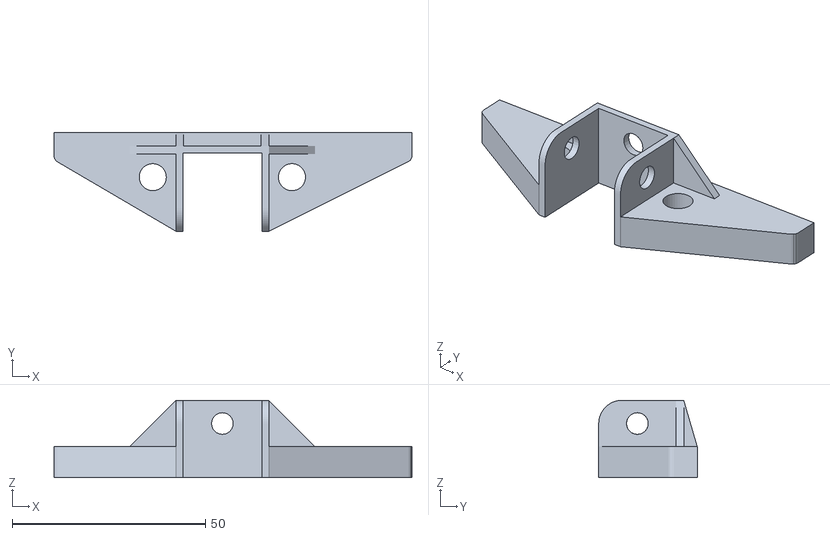
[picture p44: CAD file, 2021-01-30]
01_Mechanic/Holder_Arduino_RQ.stl
92.6 x 25.5 x 20.0

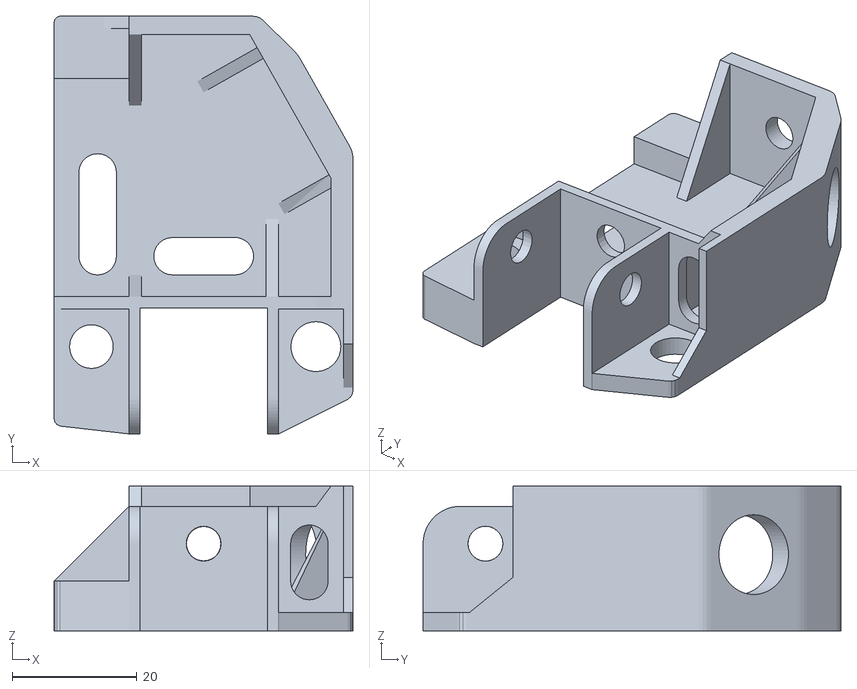
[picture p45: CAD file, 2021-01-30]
01_Mechanic/Holder_PWR_R.stl
47.9 x 67.0 x 23.3

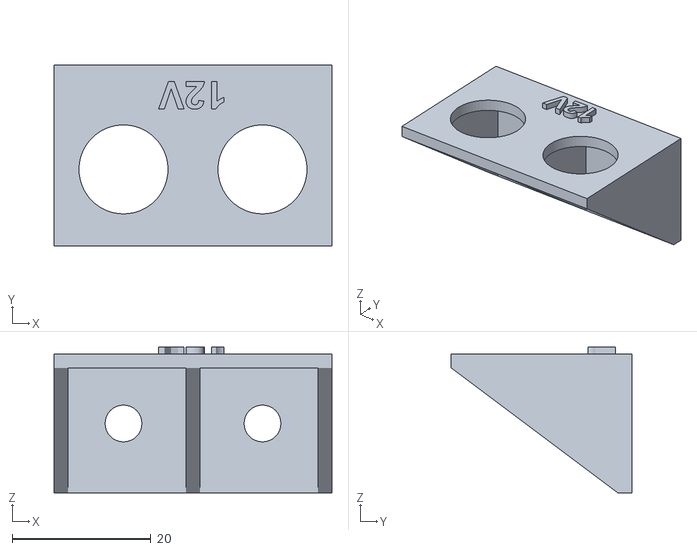
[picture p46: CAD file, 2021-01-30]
01_Mechanic/Holder_Power.stl
40.0 x 26.0 x 21.0

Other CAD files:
01_Mechanic/Cable_Clip_V.stl
01_Mechanic/Cable_Clip.stl
01_Mechanic/Holder_Cablechain_Plate.stl
01_Mechanic/Label_Supply.stl
01_Mechanic/Bolt.stl
01_Mechanic/Box.stl
01_Mechanic/Cover.stl
01_Mechanic/Holder_Arduino_LQ.stl
01_Mechanic/Holder_Display_L.stl
01_Mechanic/Holder_Display_R.stl
01_Mechanic/Holder_PWR_L.stl
01_Mechanic/Label_Name.stl
01_Mechanic/Limitblock.stl
01_Mechanic/Limitblock_Corner.stl
06_Example/test_01.skp

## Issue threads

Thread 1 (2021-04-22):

Not a Issue, but a link to the display board has not been included

MAVA916, 2021-04-22:
Good day Thomas,

Thank you for sharing your 2-AxisLaserCutter with the whole world! I'm very interested in building it for making R/C model gliders too. I found your link to your 4-AxisFoamCutter on RCgroups in the CNC section.

Again not an issue but in the Bill Of Materials their is no direct link to the display board, and tried to search the display board under bigtree-tech.com, and found nothing like in your pictures(with the red circuit board), so it must be a clone from another vendor, or a replacement part for another kind of machine.

Can you update your Github build to include the direct link to the display board?

Thank you for your work on this laser cutter.

Martin

ThomasHeb, 2021-04-22:
Hello Martin,

you are right, I linked to a wrong bundle.
I bought Arduino, Ramps, Display and Stepper Driver in one bundle, but linked one without display.

Display:
https://www.amazon.de/Redrex-Vollgrafik-Display-Controller-3D-Drucker-Arduino/dp/B01LO20XGS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

Bundle
https://de.banggood.com/Geekcreit-LCD-12864-RAMPS-1_4-Board-2560-R3-Control-Board-A4988-Driver-Kit-For-3D-Printer-p-936768.html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)
or
https://www.amazon.de/Controller-Schrittmotor-Treiber-Heatsink-Grafik-Smart-Display-Controller-3D-Drucker/dp/B01NCZ09Q5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ÅMÅŽÕÑ&dchild=1&keywords=ramps+1.4+display+arduino&qid=1619111198&s=industrial&sr=1-15
or in Germany:
https://www.roboter-bausatz.de/p/ramps-1.4-kit-12864-lcd-controller
or
https://www.roboter-bausatz.de/p/ramps-1.4-kit-12864-lcd-controller-drv8825-schrittmotoren
other Steppers, but should work, too

Best regards
Thomas

Closed 2021-04-22.

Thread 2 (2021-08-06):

XPS with laser?

neo2001cro, 2021-08-06:
ThomasHeb Hi
A see that you have dialed in your 2AxisLaserCutter to cut wood (balsa?) super, you 'cut' in one go the table to ;)
Have you maybe try to cut 3-5mm XPS, Foam with laser?

ThomasHeb, 2021-08-06:
Hello Neo,

I used to cut balsa with medium power: 3mm balsa with 40% power and 500mm/min (S40F500) and 5 repeats to cut through.
For Foam (XPS) I go with 10% power and 750mm/min (S10F750) and 5 repeats for 5mm

Regards
Thomas

neo2001cro, 2021-08-06:
Hi ThomasHeb

1x optional red and black connector on the billing list is 'dead'.?

ThomasHeb, 2021-08-06:
The connectors are just for the input voltage.... search for something like this (google: connector 4mm lab)
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

Price looks good! But be aware, that the laser cutter was a project for me (firmware, SketchUp, ...). You can buy a ready to run version for less than 300 EUR

https://de.banggood.com/search/laser-cutter.html?from=nav

neo2001cro, 2021-08-06:
Hi, ThomasHeb

Thank you for clearing 'missing' parts

:) i know that to (that there is 'redy to run' solutions), and my question is, is your Laser Cutter better then 'ready to run'?

I see that you are very smart man, so, there must be 'reason' that you have go on that 'project'. If i may ask, why ;) ?
I will try to guess, you just wanna to 'refresh' your knowledge ;) :P

ThomasHeb, 2021-08-07:
I had three reasons to go for an own build:
- I had most of the parts already here
- I wanted to do it as my own project ;P
- I wanted a solution without PC (SD Card + Display), my workbench is always dusted.

My solution is optimized for cutting only (firmware in Arduino). If you want do do engraving, especially with different shading, I would recommend to go for a ‚ready to run‘. In addition the size of the gcode will get very big for engraving (dot by dot) and therefor a PC is needed to send the gcode.

neo2001cro, 2021-08-07:
ThomasHeb Hi

i have alredy ask so many stupid ;) questions, so here goes two more ;)
Have you look on 'ready to run' solutions, do you have yours 'favorite'?
And, yours solution of working with, and from Sketchup is 'feature' that i like a lot! Respect.
So, can i use your software solution on 'ready to run'?

ThomasHeb, 2021-08-07:
Hi Neo,

I didn‘t look for ready to run solutions.

SketchUp Plugin is generating gcode, including power settings and travel speed, it is a simple text file. you can send this file via usb to any laser engraver with a universal gcode sender.

ThomasHeb, 2023-01-05:
closed due to no traffic

Closed 2023-01-05.

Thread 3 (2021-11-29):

Cutting with Lightburn does not work

ThomasHeb, 2021-11-29:
Cutting with Lightburn software https://lightburnsoftware.com does cut shapes and traveling between shapes.
Engraving does work.

ThomasHeb, 2021-11-29:
Cutting is controlled with G0 (seek, laser should be off) and G1 (laser is on) commands.
G0 did not switch off the laser. gcode.cpp changed for seeking in laser-mode.

Closed 2021-11-29.

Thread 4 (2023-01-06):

not working

melodic16, 2023-01-06:
Hey Thomas,

this is my setup, as you can see on the monitor I already upload the sketch,, but nothing happen.

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

if need more photos pls let me know.

ThomasHeb, 2023-01-06:
Good morning!
The display enclosure looks really good.
I see on your picture, that you connected DIR-, ENA- and PUL- to GND on the Arduino. This should work.
So I think, we should work through firmware and hardware to get the driver working.....

You will need the small button on the display next to the buzzer. you have a hole inside your enclosure. This button is the back button. The wheel on the display has a button, too.... this is the ok button.

**Test 1: Moving the stepper from the display**
I am not sure is you understood my operating procedure on the display, so please let me explain:
- go to the POSITION menu, as on your picture
- on the lower end of the display, you see: "> Set laser dot on/off"
- turn the wheel to the right.... the textile will disappear and you get a curser unter the Y-coordinates.
- keep turning until the curser is on the mm position.
- press the wheel to select
- turn the wheel to change the position

Sorry, it is complicated with only one wheel and two knobs.
The stepper should move a bit.....
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

**Test 2: Moving the stepper via gcode**
You can connect your laptop and start the Serial Monitor in the Arduino IDE.
Select 115200 baud and the Com-Port (you will get a reset of the arduino... that is ok)
Moving the Laser in the POSITION Menu should send "ok" over the Com-Port

You can send code commands via the Serial Monitor, too:
- G91         this sets to relative position mode
- X1           this moves the X-Axis 1mm
After each command you should get an "ok"

**Test 3: Hardware**
- please check the GND connection to DIR-, ENA- and PUL- to GND from the Arduino GND
- please check the supply voltage to the driver
- please check the motor connections. remove the connector from the driver.... you should be able to turn the motor. connect A+ and A-: you should not be able to turn the motor anymore

**Test 4: Settings**
can you upload the config.h and defaults.h file?
best pack them in a zip and attach it here

P.S. how big do you plan your laser?..... I used the smallest NEMA17 motors ;o)

Best Regards
Thomas

ThomasHeb, 2023-01-06:
Hi,
I checked your picture again. and it seems, that you connected the driver to the wrong "positions" on the Ramps 1.6 board.
you need to use the positions which are marked with E0 and E1.
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

Best Regards
Thomas

melodic16, 2023-01-06:
Hello

> Good morning! The display enclosure looks really good. I see on your picture, that you connected DIR-, ENA- and PUL- to GND on the Arduino. This should work. So I think, we should work through firmware and hardware to get the driver working.....
>
> You will need the small button on the display next to the buzzer. you have a hole inside your enclosure. This button is the back button. The wheel on the display has a button, too.... this is the ok button.

Yes, I have that button maybe to small on the pic so it's like hole

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

Yes I understand and don't say sorry you are already helping me alot. I already try this but my motors not moving

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

Ok I will try this

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

Ok

>
> P.S. how big do you plan your laser?..... I used the smallest NEMA17 motors ;o)

I use nema34, it is quite big, the length of X axis is 5meters and Y axis is 2meters
I am not add the laser yet, just want to see the axis work 1st

>
> Best Regards Thomas

sorry about your 2nd comments, so I should connect the driver to X axis to E0 and Y axis to E1?

ThomasHeb, 2023-01-07:
Good morning!
X axis goes to E0, Y axis goes to E1.

Sorry this may be a bit confusing from the hardware connection perspective. This is a result of the shared code with the foam cutter. I am a bit afraid of changing the code, because I would need to do all the tests on both devices (laser and foam) again….. you know… never change a running system.

I would ask you to change the connection to E0 and E1.

You do not need to worry from the software side or from the gcode perspective. axis are controlled with X and Y and I did a successful test with light burn software, too.

Your dimensions are amazing. I would appreciate, if you share some pictures.
All the best for your project.

Best Regards
Thomas

melodic16, 2023-01-09:
Hello Thomas,

> Good morning!
> X axis goes to E0, Y axis goes to E1.

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
and if I add limit switch, the red is for x axis and yellow for y axis?

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

Done, okay now my motors working. But somehow its skipping step/stalling at the start and the end of the rotation.
https://user-images.githubusercontent.com/122068445/211240495-84a9e661-aca4-405d-bc6a-c981f6cbfdd3.mp4
Sorry motor so rusty
I am very newbie on this kind of thing
here the setting of the driver
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

>
> Your dimensions are amazing. I would appreciate, if you share some pictures.
> All the best for your project.

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

thank you

melodic16, 2023-01-09:
Hello Thomas,

> Good morning!
> X axis goes to E0, Y axis goes to E1.

and if I want add limit switch I put on the default location? 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

Done, okay now my motors working. But somehow its skipping step/stalling at the start and the end of the rotation.
https://user-images.githubusercontent.com/122068445/211240495-84a9e661-aca4-405d-bc6a-c981f6cbfdd3.mp4
Sorry motor so rusty
I am very newbie on this kind of thing
here the setting of the driver
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

>
> Your dimensions are amazing. I would appreciate, if you share some pictures.
> All the best for your project.

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

thank you

melodic16, 2023-01-09:
Hello Thomas,

> Good morning!
> X axis goes to E0, Y axis goes to E1.

and if I want add limit switch I put on the default location? 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

Done, okay now my motors working. But somehow its skipping step/stalling at the start and the end of the rotation.
https://user-images.githubusercontent.com/122068445/211240495-84a9e661-aca4-405d-bc6a-c981f6cbfdd3.mp4
Sorry motor so rusty
I am very newbie on this kind of thing
here the setting of the driver
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

>
> Your dimensions are amazing. I would appreciate, if you share some pictures.
> All the best for your project.

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
here you can see my project

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

thank you

melodic16, 2023-01-09:
Hello Thomas

I already fix the skipping step/stalling at the start and the end of the rotation. I put the wrong cable on the driver, my bad.

ThomasHeb, 2023-01-09:
Hello,

for the Limit switches check out the Hardware chapter
https://github.com/ThomasHeb/2AxisLaserCutter/tree/main/02_Hardware

melodic16, 2023-01-24:
Hi Thomas, sorry for late reply, I just work on another project.

I just add the 100nF
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

ThomasHeb, 2023-01-24:
Helle, this is Not Vorrecht. In Homing Cyclones a Limit Switch should stop the motor and lead to some position movements. Please trigger the limit switch manually and check if your 5V is stable

ThomasHeb, 2023-01-25:
Hello, I don't have these limit switch pcbs from makerbot here for testing. but never the less, the schematic should be like this.
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
with this wiring and connection on your board, you connect black to green, when triggering. this means + / - or 5V and GND are connected directly.... this causes the voltage drop and CPU will restart after releasing the limit switch (please do not do this, this may damage your voltage regulator on the arduino board).

these limit switches operate as normal open (NO).... the firmware requires NC. is you have a broken cable, NO switch would not detect a limit, because of that safety reason I only use (and implemented) NC.

you can modify your limit switches, but the LEDs will not work:
- easy way, LED not working: connect green cable to S and red cable to -. Do not connect black cable

- cool way, LED should work: connect green cable to S and red cable to - and black cable to +. rotate the LED (remove from boards and change pads/pins).
[Bildschirmfoto 2023-01-25 um 17.24.24.pdf](https://github.com/ThomasHeb/2AxisLaserCutter/files/10501649/Bildschirmfoto.2023-01-25.um.17.24.24.pdf)
- Please verify connection on Ramps carefully... position of red and green wire must be inverted and connector must be flipped

Closed 2023-11-15.

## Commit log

2021-04-22 Update readme.md
    Update BOM with correct link to "Arduino, Ramps, Stepper, Display" bundle.
2021-11-29 Update gcode.cpp for laser-mode
    G0 commands for seeking with laser off implemented (for use with Lightburn software)
